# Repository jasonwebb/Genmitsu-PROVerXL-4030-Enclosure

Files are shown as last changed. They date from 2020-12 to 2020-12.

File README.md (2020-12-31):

# Genmitsu PROVerXL 4030 Enclosure
Parts lists and CAD files for a DIY aluminum extrusion enclosure with a slide-out drawer for the 4030 CNC router.

## Parts lists:

<ul>
  <li><a href="Parts lists/Enclosure.csv">Enclosure parts list</a></li>
  <li><a href="Parts list/Table.csv">Table parts list</a></li>
</ul>

## Fusion360 project files
All designs and drawings made with version 2.0.9052.

<ul>
  <li><a href="Fusion360 project files/Enclosure.f3d">Enclosure</a></li>
  <li><a href="Fusion360 project files/Table.f3d">Table</a></li>
</ul>

## Important assembly notes

1. The flanged button head screws sourced for attaching the drawer slides to the aluminum extrusion rails don't quite fit through the holes/slots in some of the drawer slide tracks. Use a 1/2" drill bit to widen these slots just enough for the screw heads to fit through.

1. Be sure to add a diagonal 2x4 beam under the table surface, as shown in the 2x4Basic's (legs) assembly manual. Double check the length needed, but I _think_ it was 50".

1. Be very careful when attaching the inner drawer slide tracks to the sliding MDF base! Pre-drill the holes using the tracks as a template. Make sure the tracks are aligned correctly so they match the slides on the frame. Drill and screw them as close as possible to the center of the board to minimize risk of delaminating the board later. Use either MDF or particle board - layered plywood may separate.

1. Use a 2-3/8" hole saw to drill a hole for the furniture grommet on the table surface near the back of the enclosure. Make absolutely sure that you're not drilling into the diagonal 2x4 crossbeam!

## Things to improve later

1. The bottom of the enclosure is left open, which can increase the noise level you hear outside the enclosure. Try putting some foam under the sliding base to block some of this.

1. Dust collection could be added by installing a vacuum on the bottom shelf and routing a hose up into the enclosure through the table surface.

1. The front door seal is a bit thick and requires significant pressure to compress enough for good sound reduction. Might be worth trying out different approaches for sealing.

1. I have not yet figured out a good way to add latches for closing and sealing the front door. For now I'm just using wood clamps.

## Renders

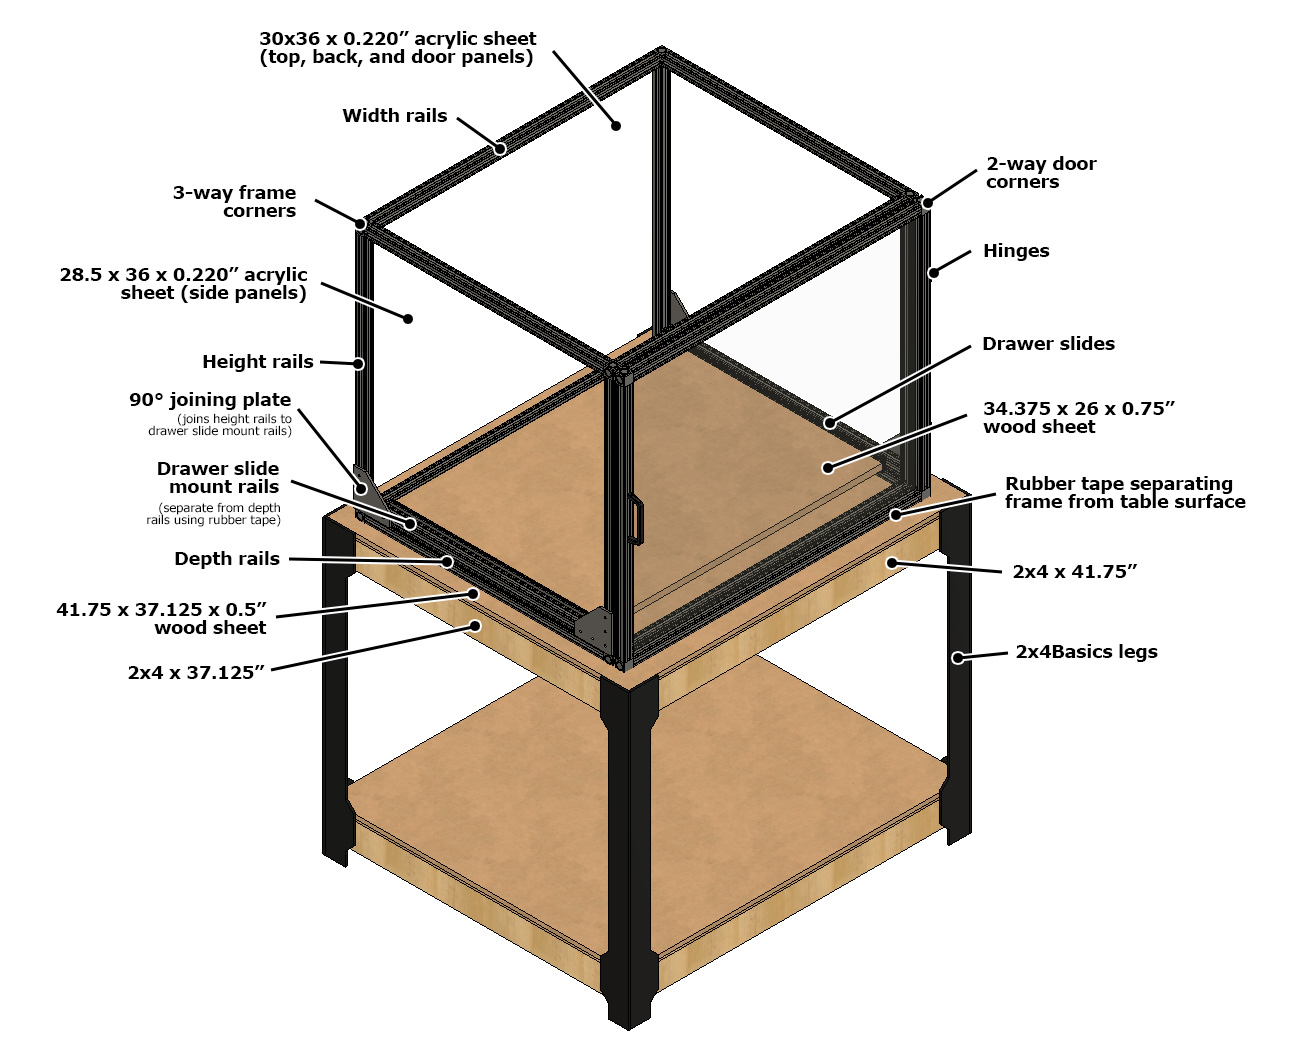
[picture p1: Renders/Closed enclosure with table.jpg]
Annotated drawing of enclosure on top of table from an isometric top-left view.


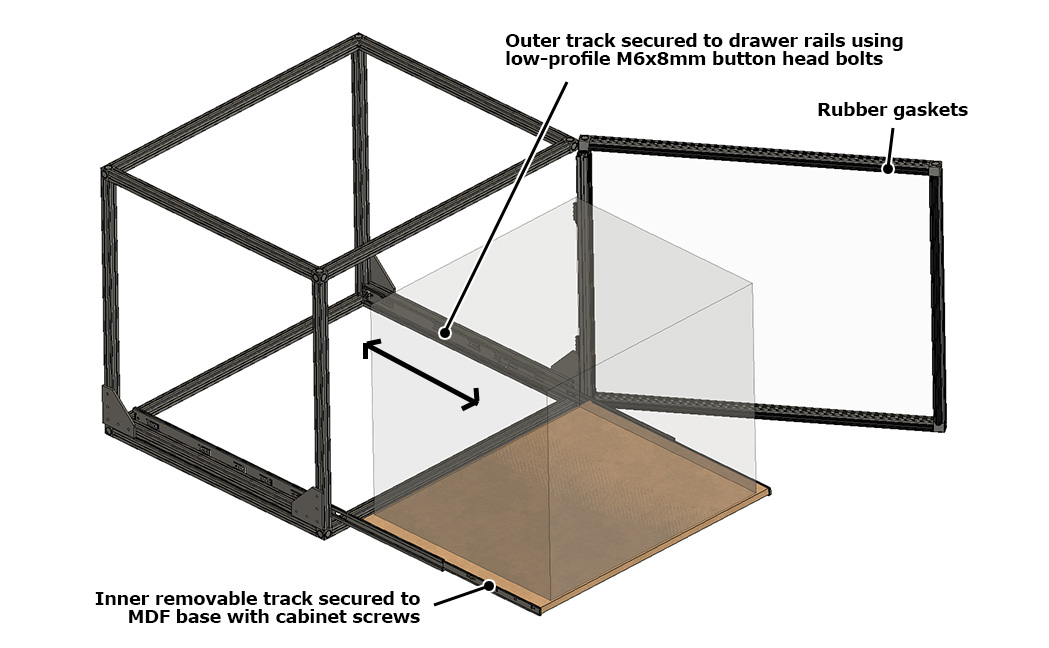
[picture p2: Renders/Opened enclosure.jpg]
Annotated drawing of enclosure with front door swung open and sliding base extended.


## Photos

<table width="100%">
  <tr>
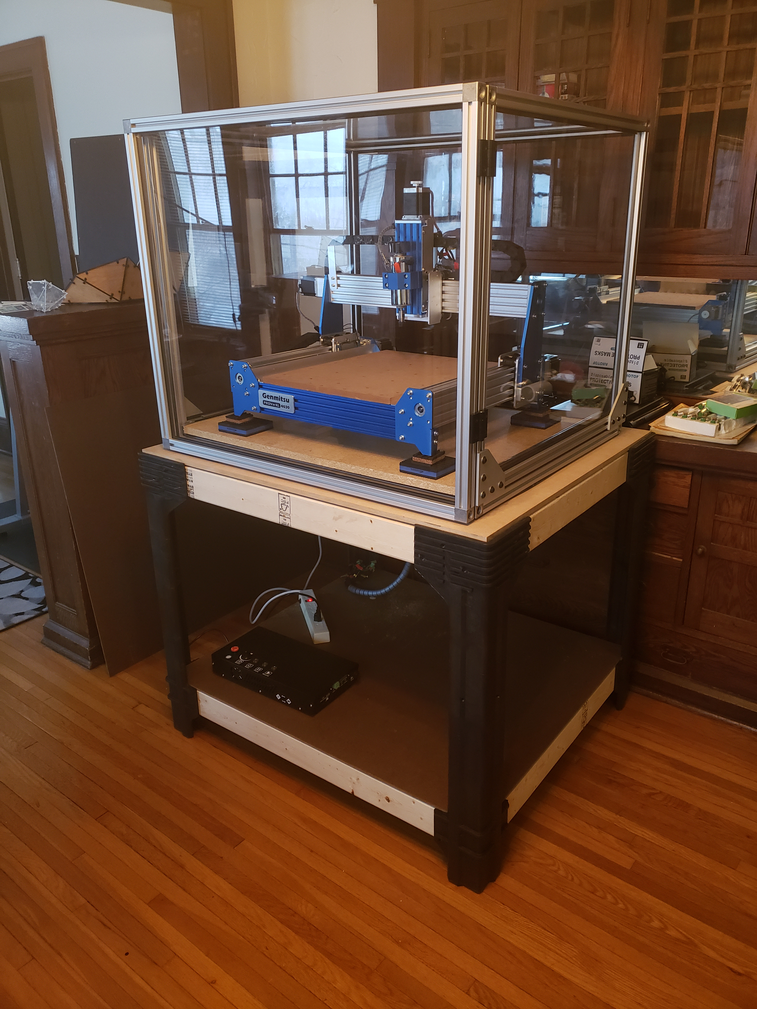
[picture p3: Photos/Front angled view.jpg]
    <td width="50%"></td>
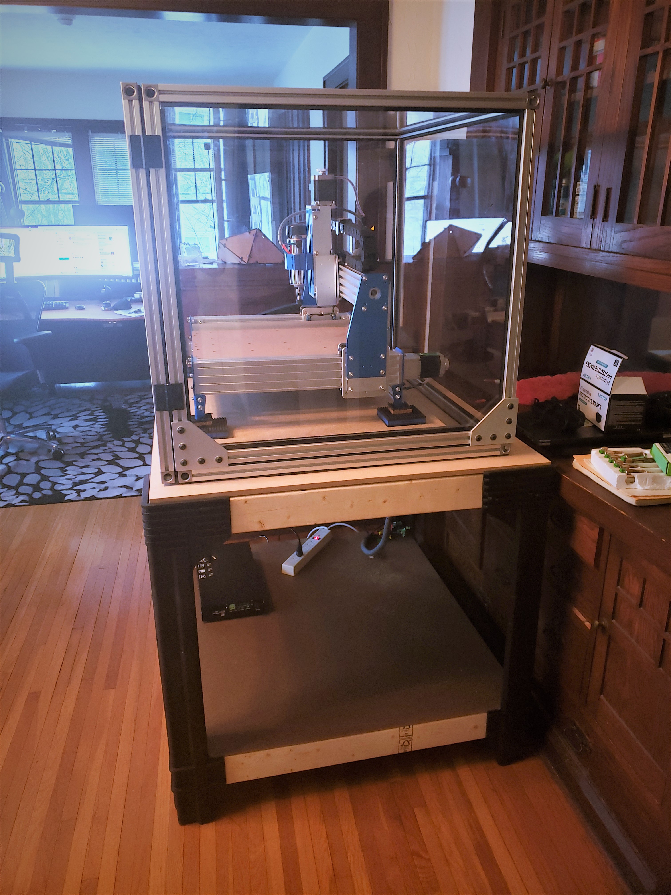
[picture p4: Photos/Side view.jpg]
    <td></td>
  </tr>
</table>

## Drawings

### Outer dimensions

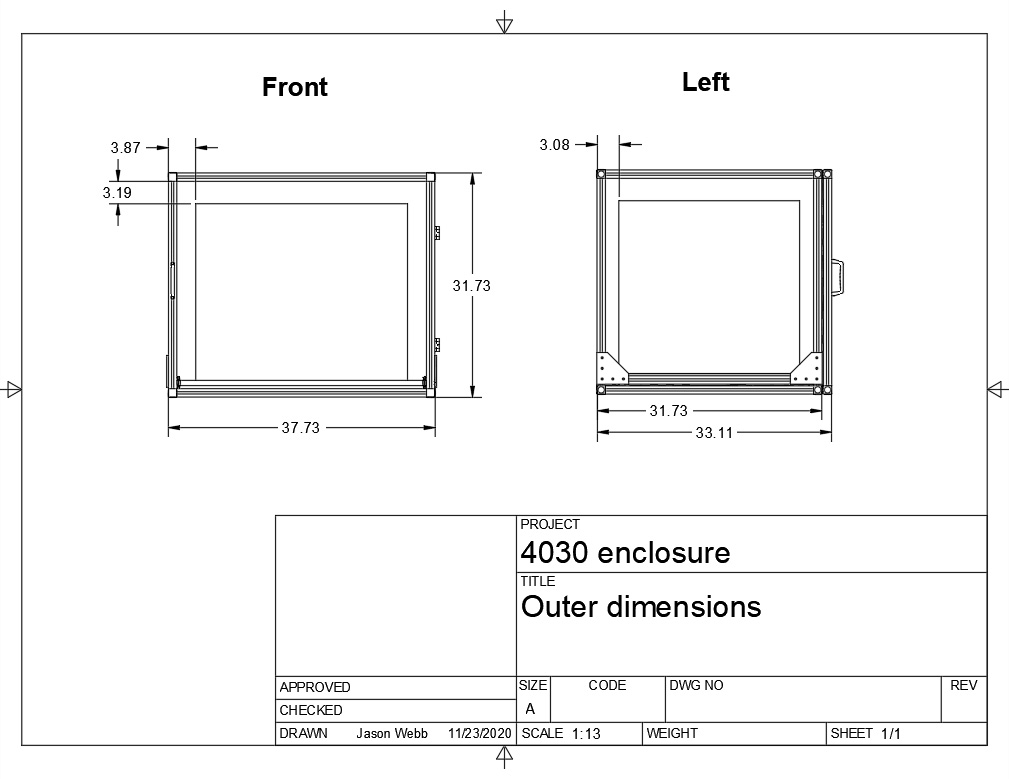
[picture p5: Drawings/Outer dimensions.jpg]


### Aluminum extrusion dimensions

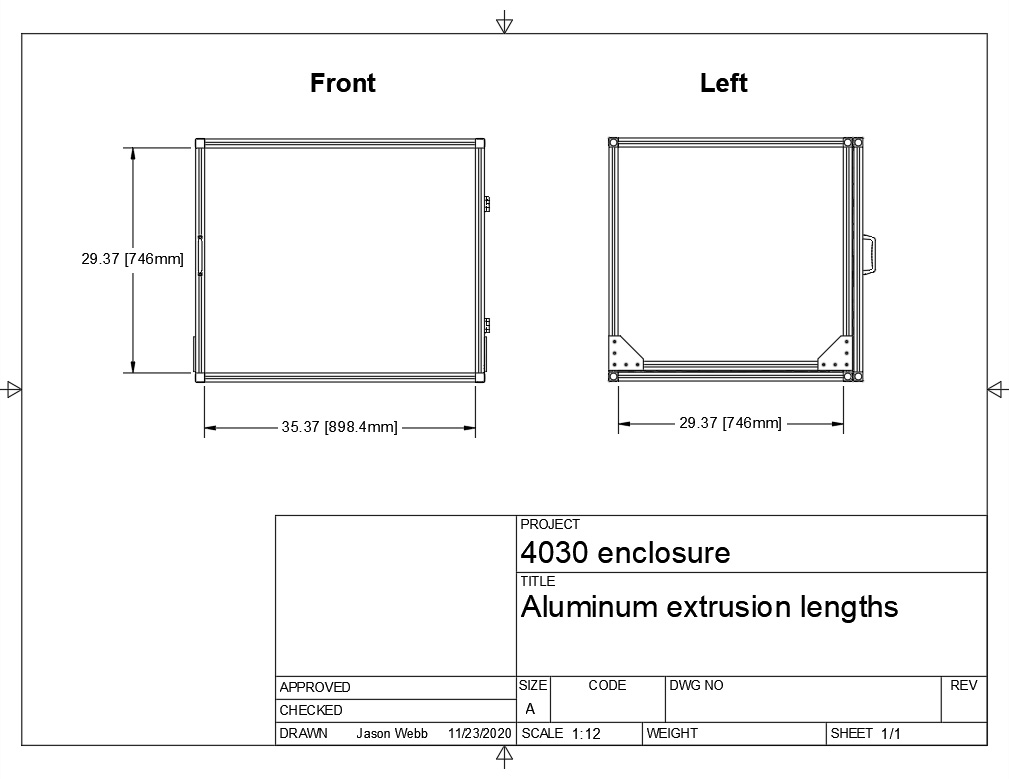
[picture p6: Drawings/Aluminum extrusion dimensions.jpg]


### Sliding base dimensions

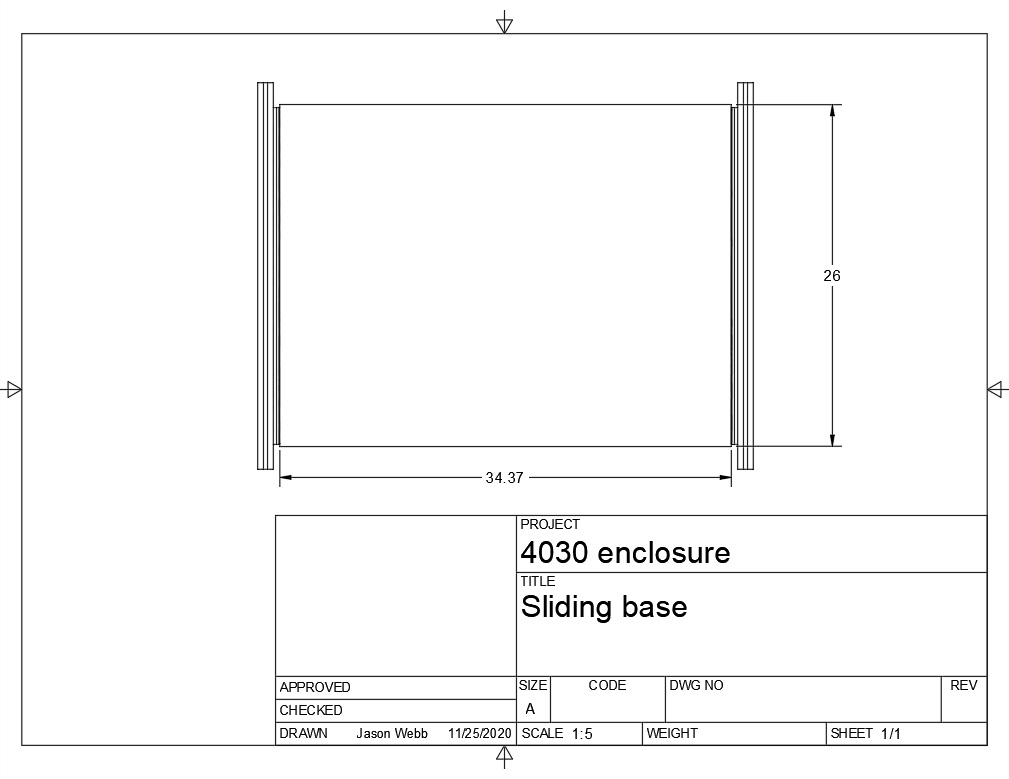
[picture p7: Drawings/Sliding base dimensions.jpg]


### Table

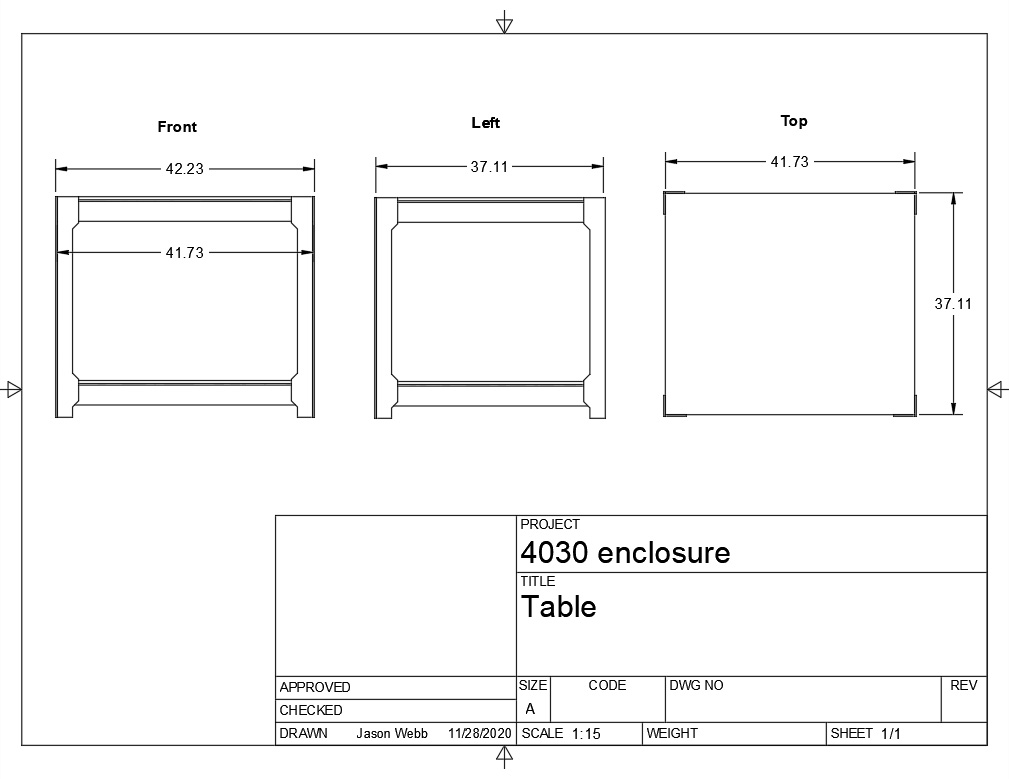
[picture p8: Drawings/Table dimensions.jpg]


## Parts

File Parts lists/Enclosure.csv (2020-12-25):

Sub-assembly | Part | Purpose | Qty | Price ea. | Sub-total | Source | URL | Note
Frame | 30mm aluminum extrusion - 35.375" | Width rails | 4 | $7.63 | $30.52 | T-Nutz | https://www.tnutz.com/product/exm-3030/?attribute_pa_length-in=35&attribute_pa_fractional-length=0-375-3-8 | Opt for M8 x 1.25 x 30mm taps on both ends
 | 30mm aluminum extrusion - 29.375" | Height rails | 4 | $6.58 | $26.32 | T-Nutz | https://www.tnutz.com/product/exm-3030/?attribute_pa_length-in=29&attribute_pa_fractional-length=0-375-3-8 | Opt for M8 x 1.25 x 30mm taps on both ends
 | 30mm aluminum extrusion - 29.375" | Depth rails | 4 | $6.58 | $26.32 | T-Nutz | https://www.tnutz.com/product/exm-3030/?attribute_pa_length-in=29&attribute_pa_fractional-length=0-375-3-8 | Opt for M8 x 1.25 x 30mm taps on both ends
 | 3-way corner connector with bolts | Frame corners | 8 | $4.25 | $34.00 | T-Nutz | https://www.tnutz.com/product/cbc-030-3d/
 | Rubber tape (19/32" W x 5/16" H x 10' L) | Isolates frame from table surface | 1 | $7.96 | $7.96 | Menard's | https://www.menards.com/main/hardware/weather-stripping/19-32-x-5-16-x-10-rubber-auto-marine-weather-strip/52021/p-1459185067252-c-3624.htm
Door | 30mm aluminum extrusion - 35.375" | Top and bottom rails | 2 | $7.63 | $15.26 | T-Nutz | https://www.tnutz.com/product/exm-3030/?attribute_pa_length-in=35&attribute_pa_fractional-length=0-375-3-8 | Opt for M8 x 1.25 x 30mm taps on both ends
 | 30mm aluminum extrusion - 29.375" | Left and right rails | 2 | $6.58 | $13.16 | T-Nutz | https://www.tnutz.com/product/exm-3030/?attribute_pa_length-in=29&attribute_pa_fractional-length=0-375-3-8 | Opt for M8 x 1.25 x 30mm taps on both ends
 | 2-way corner connector with bolts | Door corners | 4 | $4.25 | $17.00 | T-Nutz | https://www.tnutz.com/product/cbc-030-2d/
 | Steel black powder-coated heavy-duty hinge kit | Hinges | 2 | $8.25 | $16.50 | T-Nutz | https://www.tnutz.com/product/hi-015/ | Opt for the (4) M6 x 16mm screws and drop-in T-nuts
 | Black plastic handle with hardware (medium size) | Handle | 1 | $3.43 | $3.43 | T-Nutz | https://www.tnutz.com/product/han-015/
Sliding base | Aluminum extrusion - 29.375" | Mounts for drawer slides | 2 | $6.58 | $13.16 | T-Nutz | https://www.tnutz.com/product/exm-3030/?attribute_pa_length-in=29&attribute_pa_fractional-length=0-375-3-8 | Opt for M8 x 1.25 x 30mm taps on both ends
 | 26", 70lb capacity slides (pair) | Drawer slides | 1 | $23.00 | $23.00 | McMaster-Carr | https://www.mcmaster.com/catalog/11435A29 | Two slots on each slide need to be manually enlarged with 1/2" drill bit to fit the flanged button head mounting screws
 | Rubber tape (19/32" W x 5/16" H x 10' L) | Seals between rails | 1 | $7.96 | $7.96 | Menard's | https://www.menards.com/main/hardware/weather-stripping/19-32-x-5-16-x-10-rubber-auto-marine-weather-strip/52021/p-1459185067252-c-3624.htm
 | M6 x 8mm flanged button head screws (25pk, only 12 needed) | Mounts drawer slides to mount rails | 1 | $7.70 | $7.70 | McMaster-Carr | https://www.mcmaster.com/catalog/92137A523
 | M6 T-nut for 30mm rail with spring-ball | Mounts drawer slides to mount rails | 12 | $0.50 | $6.00 | T-Nutz | https://www.tnutz.com/product/db-015/?attribute_pa_thread-size=m6-x-1-0
 | #8 x 2-1/2" wafer head cabinet screws | Connects sliding wood platform to drawer slides | 1 | $8.38 | $8.38 | Menard's | https://www.menards.com/main/hardware/fasteners-connectors/screws/cabinet-screws/spax-reg-8-x-2-1-2-t-star-plus-drive-yellow-zinc-wafer-head-cabinet-screw-1-l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
 | 15 Series 5 hole 90 degree joining plate | Connects the drawer slide mount rails to the height rails | 4 | $5.00 | $20.00 | T-Nutz | https://www.tnutz.com/product/jp-015-h/ | Opt for 5/16-18 x 5/8" screws with double and triple economy T-nuts
 | Latches | Firmly closes door and compresses inner door seal |  |  | $0.00
Panels | 30x36 x 0.220" acrylic sheet (4pk) | Back, top, and side panels | 1 | $189.75 | $189.75 | HD Supply | https://hdsupplysolutions.com/p/acrylic-sheets-00-145-5/plaskolite-30x36-acrylic-sheet-package-of-4-p737606 | Cut ~6mm off each corner to fit into corner brackets. Cut side panels down to 28.5x30"
 | 30x36 x 0.220" acrylic sheet | Door panel | 1 | $65.98 | $65.98 | Menard's | https://www.menards.com/main/doors-windows-millwork/acrylic-glass-sheets/amerilux-0-220-thick-clear-acrylic-sheets/cla18x24x220/doors-windows-millwork/acrylic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 | Cut ~6mm off each corner to fit into corner brackets.
 | Economy panel gasket - 17m (53ft) (10x30in, 6x36in) | Wedges between acrylic panels and aluminum extrusion rails to hold in place and reduce vibrations. | 17 | $1.75 | $29.75 | 8020 | https://8020.net/40-2115.html
 | T-slot inline bulb seal - 11ft (2x30in, 2x36in) | Inner door seals | 2 | $8.56 | $17.12 | McMaster-Carr | https://www.mcmaster.com/catalog/47065T814
 |  |  |  | Total | $579.27

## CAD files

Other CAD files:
Fusion360 project files/Enclosure.f3d
Fusion360 project files/Table.f3d

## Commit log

2020-12-25 Adding enclosure parts list and first annotated illustration
    [Parts list - enclosure.csv]
2020-12-29 Adding renders, drawings, Fusion360 files; reorg with better folders
    [Enclosure.csv, Enclosure.f3d, Table.f3d]
2020-12-30 Adding some assembly notes
